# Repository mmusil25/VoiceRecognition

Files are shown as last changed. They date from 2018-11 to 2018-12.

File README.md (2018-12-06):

# Voice Recognition Lock Box

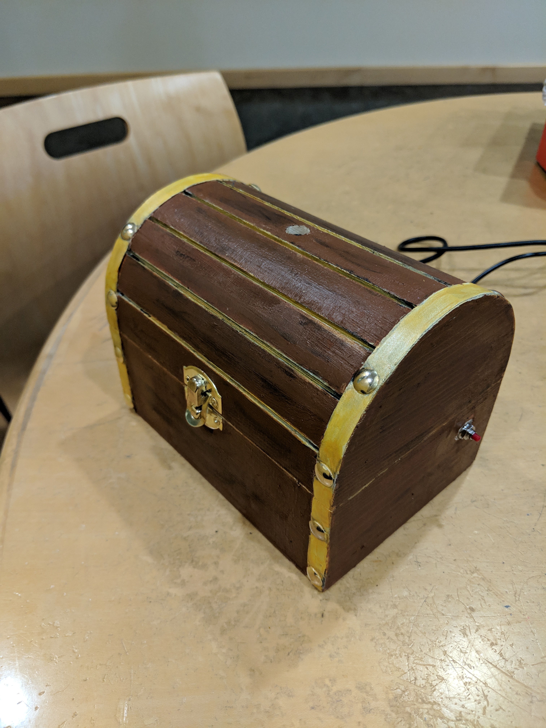
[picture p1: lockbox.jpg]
The Finished Lockbox


### Team Members

Mark Musil (mmusil@pdx.edu), Amanda Voegtlin (voegtlin@pdx.edu), Samantha Fink (scleary@pdx.edu), Rawan Abdo (rabdo@pdx.edu)

## Project Description

For the Portland State University pre-capstone class (ECE 411) the team designed a voice-activated lockbox that can be used to protect belongings. Using the open source [speech-to-text library uSpeech] (https://github.com/arjo129/uSpeech) an AtMega32U4 was programmed to activate a solenoid in response to the diction of a password ("shore"). The potential market for such a product is adolescents with small belongings such as jewelry or diaries that they wish to protect. 

Please see the presentation file "Presentation_Group3.pdf" for a thorough description including block diagrams, functional flowcharts and more.

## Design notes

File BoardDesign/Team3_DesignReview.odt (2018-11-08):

Schematic and Board Layout Design Review Notes

TEAM BEING REVIEWED: TEAM #3

REVIEWING TEAM: TEAM #11

DATE: 11/7/18

Note: (D) = dealt with

- SCHEMATIC
  - CRITICAL
    - (D) Junction dot out of RESET microprofessor button
    - (D) RESET needs a 10k pull up
    - (D) What is UVCC?
    - (D) Add 100nF caps to VCC,VCC1,AVCC,AVCC1
    - (D) Double check UCAP
    - Microphone
    - (D) How much current does the servo need?
    - (D) Remove the regulator
    - (D) Use a wall wart for the servo
      - If using wall wart to power board, need diode from processor to servo.
    - Confirm HWB function and confirm current wiring is correct.
  - MAJOR
    - (D) Add value/name to IC1
    - (D) Use 1 – 3 mA for the LEDs
    - Rearrange wires and add busses for readability.
  - MINOR
    - (D) Change font to info layer
    - (D) Go for right angles
    - (D) Do I need a buffer for the microphone output? Is that output 0 – 3.3V? Check datasheet
    - Statement “all surface mount components are …”
    - Does it use arduino?
    - Test Points Everywhere
    - Label VCC as 5V
- LAYOUT
  - CRITICAL
    - Determine if VCC line width is correct.
    - Align N$13 signal wire to lead straight into pin on processor.
  - MAJOR
    - Move/re-arrange some wires for readability.
  - MINOR
    - None.
- Bill of Materials (BOM)
  - No issues

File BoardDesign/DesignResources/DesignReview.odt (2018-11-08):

Schematic and Board Layout Design Review Notes

TEAM BEING REVIEWED: Team 3

REVIEWING TEAM: Andrew Greenberg (Schematic)/

DATE: November 1st, 2018

Instructions:

1. Reviewed team explains the concept of operation of the project.
2. Reviewer reads through schematic, layout, and BOM attempting to answer basic questions such as: what is the power supply? What is this IC and what does it do? Does the layout make sense?
3. Reviewer reads through schematic, layout, and BOM looking for best practices, such as: Are there enough bypass caps? Are the traces the right thickness?
  a. Reviewers are encouraged to use the Schematic and Layout Checklists that are posted on the D2L site.
4. One person on the reviewed team interacts and answers reviewer’s questions. A different person on the reviewed team takes notes, organized in the format below.
  Note: (D) = dealt with
- SCHEMATIC
  - CRITICAL
    - (D) Junction dot out of RESET microprofessor button
    - (D) RESET needs a 10k pull up
    - (D) What is UVCC?
    - (D) Add 100nF caps to VCC,VCC1,AVCC,AVCC1
    - (D) Double check UCAP
    - Microphone
    - (D) How much current does the servo need?
    - (D) Remove the regulator
    - (D) Use a wall wart for the servo
  - MAJOR
    - (D) Add value/name to IC1
    - (D) Issue 2
  - MINOR
    - (D) Change font to info layer
    - (D) Go for right angles
    - (D) Do I need a buffer for the microphone output? Is that output 0 – 3.3V? Check datasheet
    - (D) Test Points Everywhere
    - (D) Label VCC as 5V
    - Add note saying “All caps are ….”
- LAYOUT
  - CRITICAL
    - Issue 1
    - Issue 2
  - MAJOR
    - Issue 1
    - Issue 2
  - MINOR
    - Issue 1
    - Issue 2
- Bill of Materials (BOM)
  - Issue 1
  - Issue 2

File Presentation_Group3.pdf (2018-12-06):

# Voice Recognition Project Team #3

ECE 411 Practicum
Mark Musil, Rawan Abdo, Samantha Fink, Amanda Voegtlin

### Overview of Problem

- Adolescents want to secure small items in their home but can not find anywhere to do so.
- Must be secure enough for small keepsakes, diaries, etc.
- Not a high security system.
- Must be secure and trendy.

### Project Choice Decision Matrix

| Option 1 - Voice Activated Lock Box | Option 2 -Theremin Lock | Option 3 -Ocarina Lock | Option 4 -Rhythm Lock
Doability (Hardware) | 8 | 7 | 8 | 4
Doability (Software) | 5 | 5 | 7 | 6
Affordability | 8 | 6 | 6 | 5
Interest | 9 | 5 | 8 | 5
Prior Experience | 7 | 5 | 6 | 4
Sum | 37 | 28 | 35 | 24
Rank | 1 | 3 | 2 | 4
Status | Chosen | No | No | No

### Concept of Operation - Voice Activated Lockbox

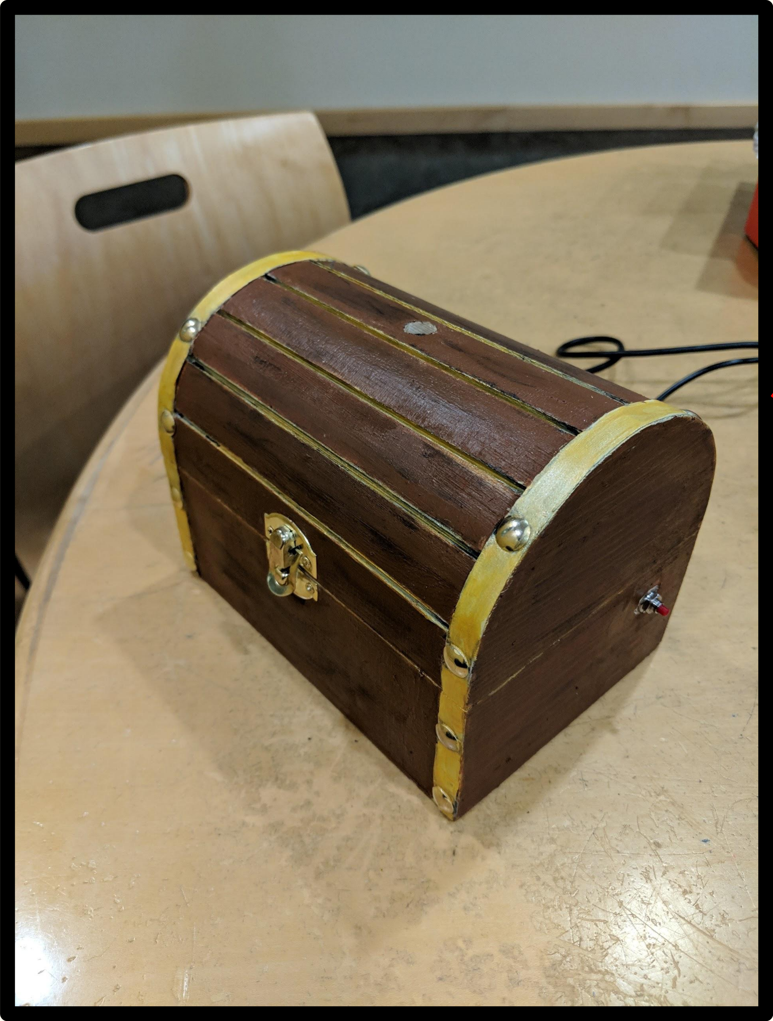
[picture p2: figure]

1. Locked state: Solenoid keeps lid
closed.
2. User input: Password spoken into microphone
3. Device output: Solenoid retracts and box is open
4. User input: Close box, press reset switch, solenoid engages lock.

User Input:
“Shore”

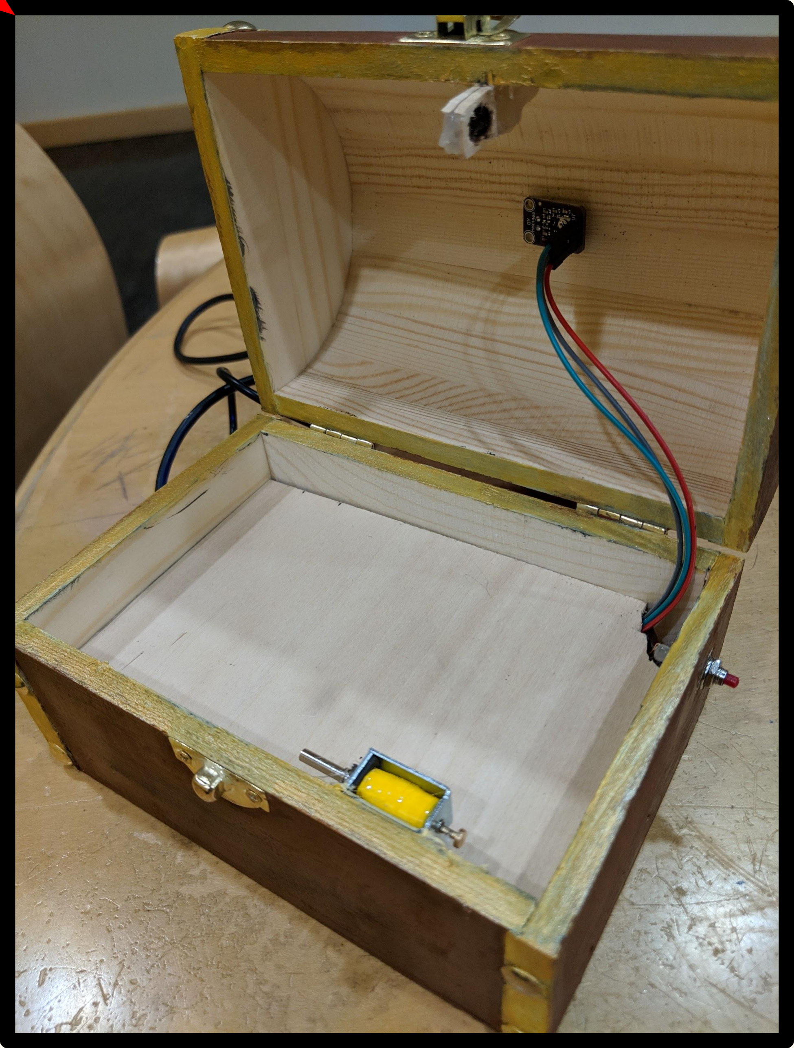
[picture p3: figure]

### Level 0 Block Diagram

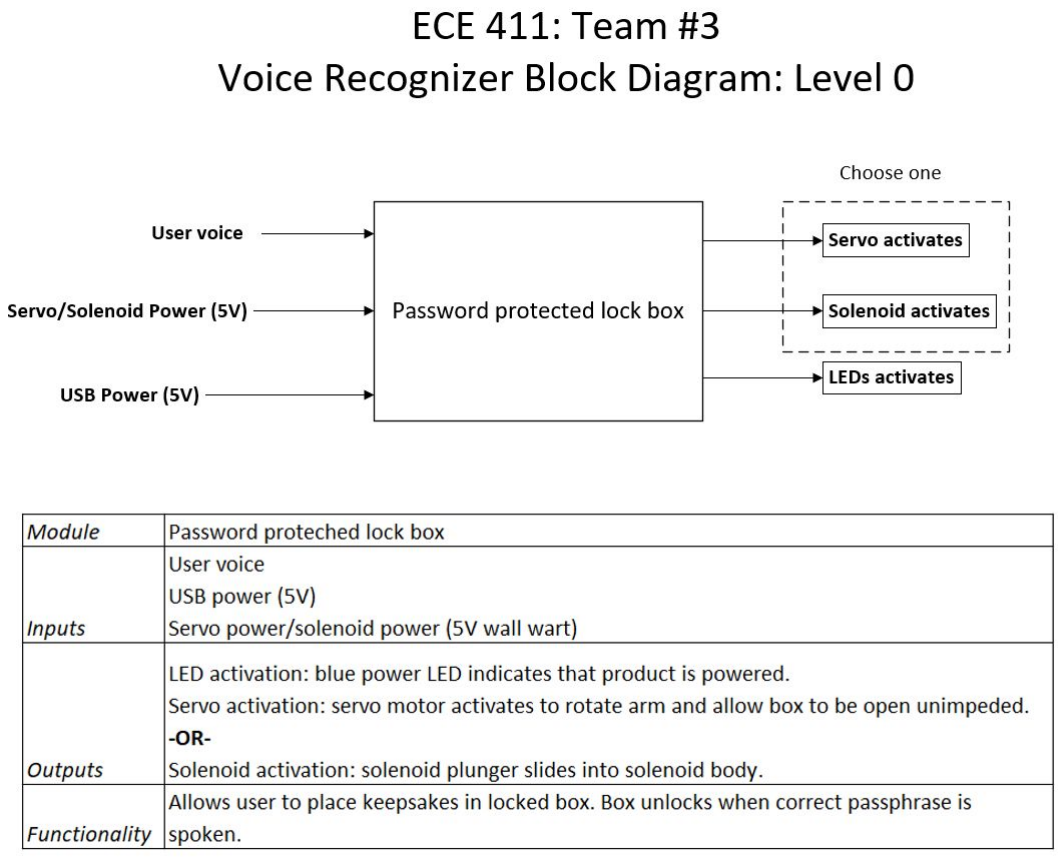
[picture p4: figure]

### Level 1 Block Diagram

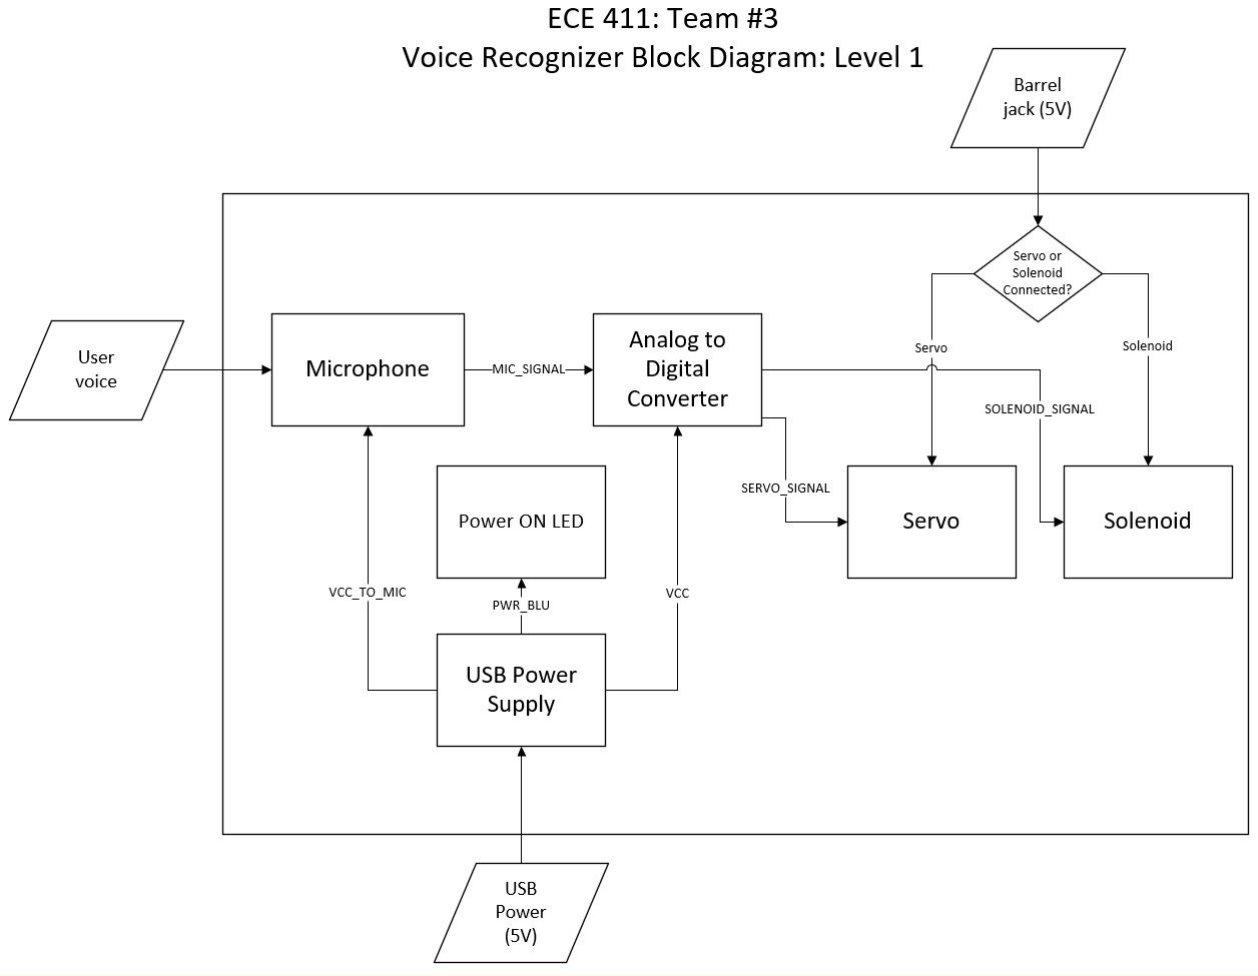
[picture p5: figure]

### Overview of Schematic - Full Picture

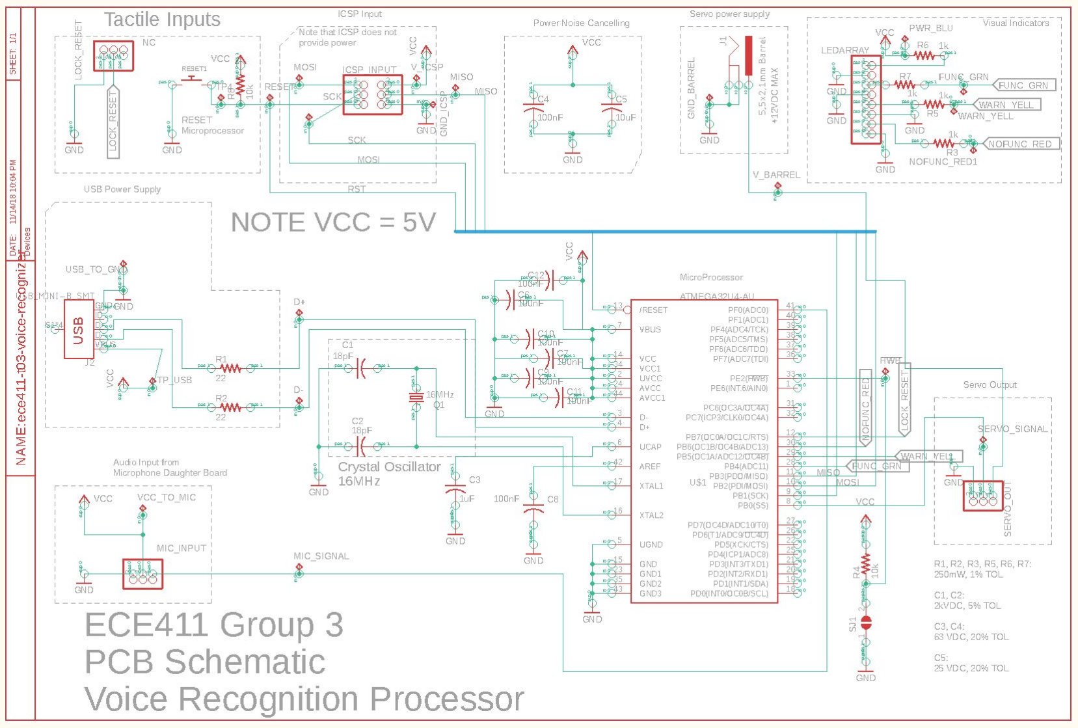
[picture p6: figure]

### Overview of Schematic - Power

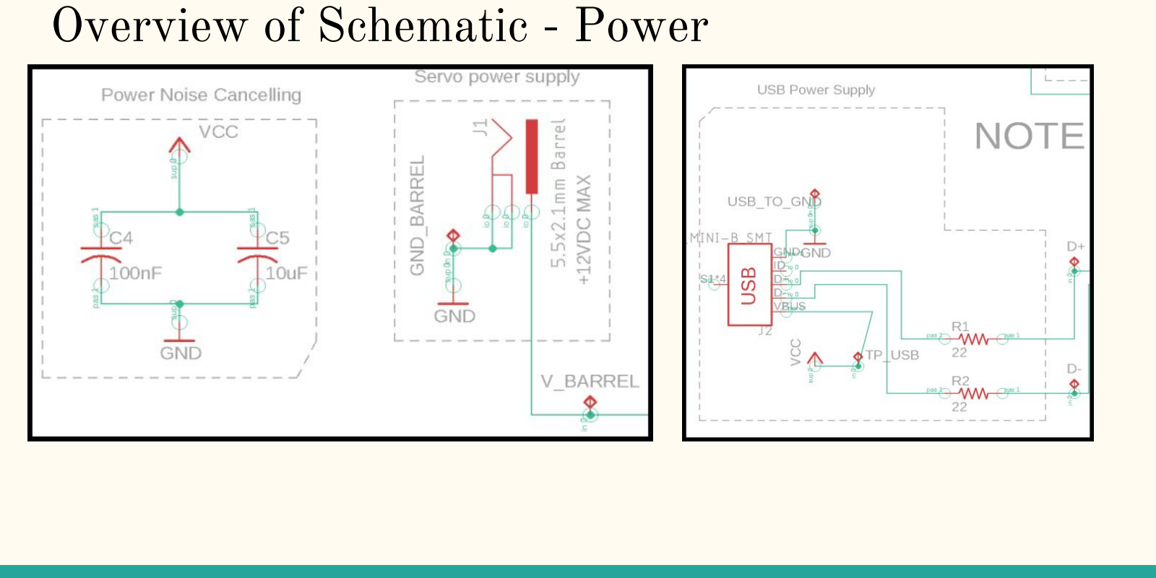
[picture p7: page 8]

### Overview of Schematic - Programming Interface

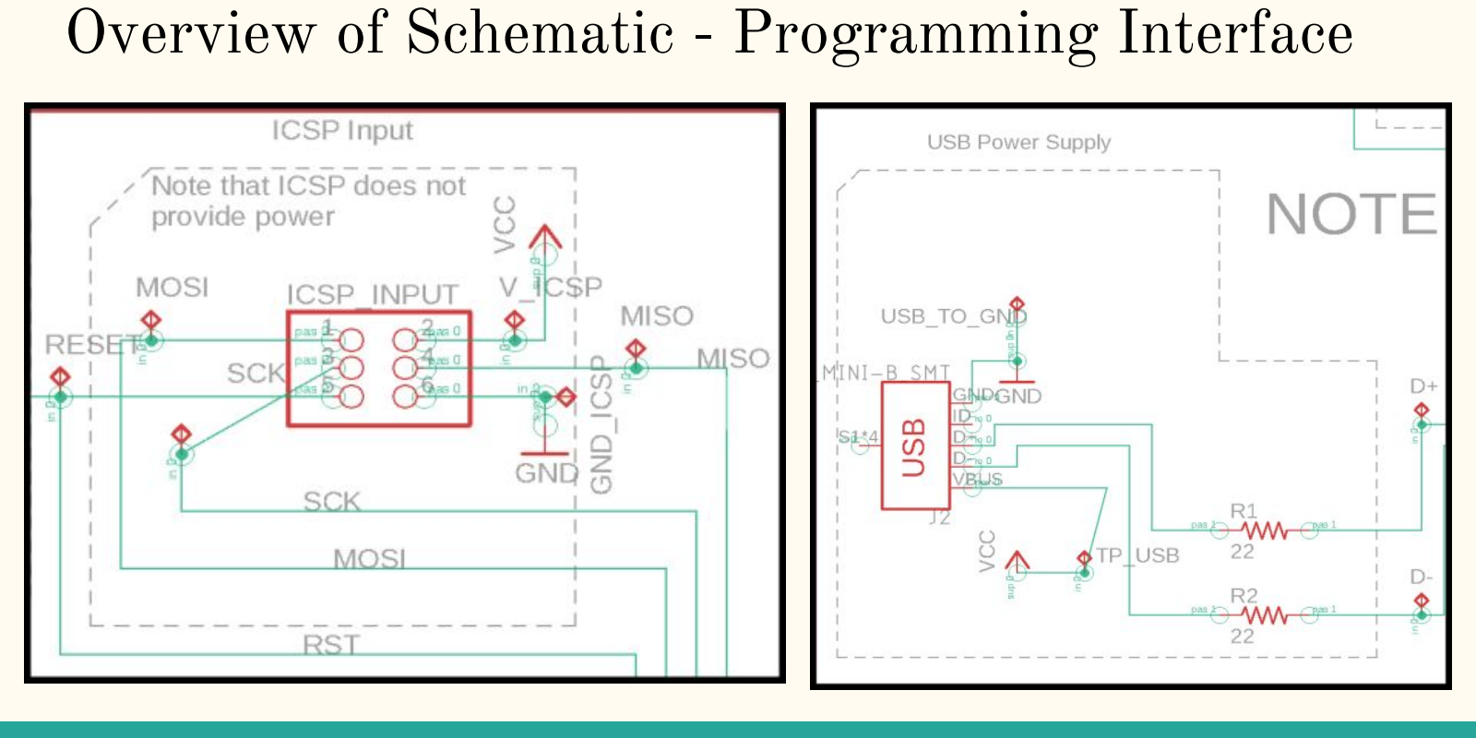
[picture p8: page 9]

### Overview of Schematic - Inputs

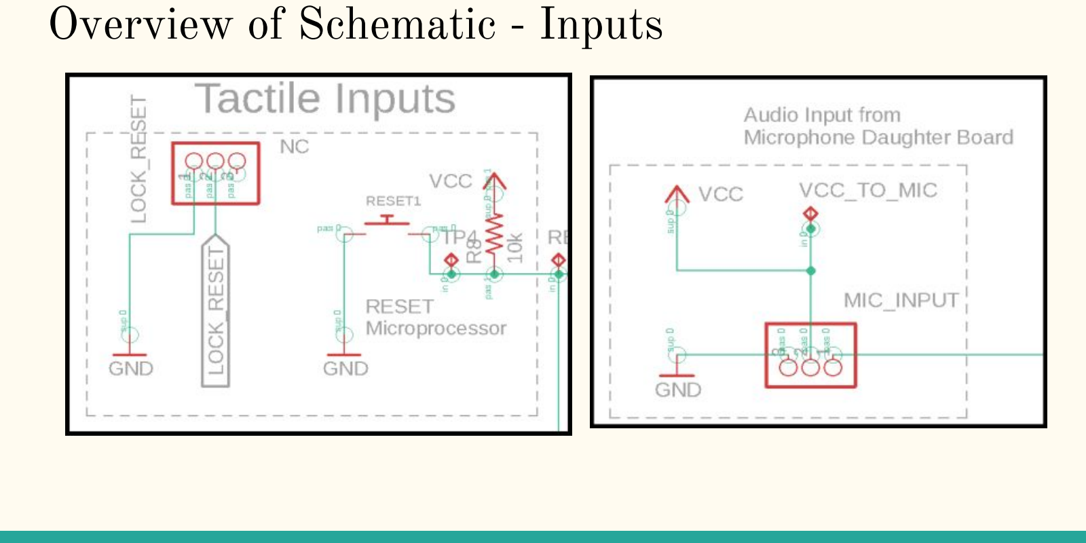
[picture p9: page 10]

### Overview of Schematic - Processor

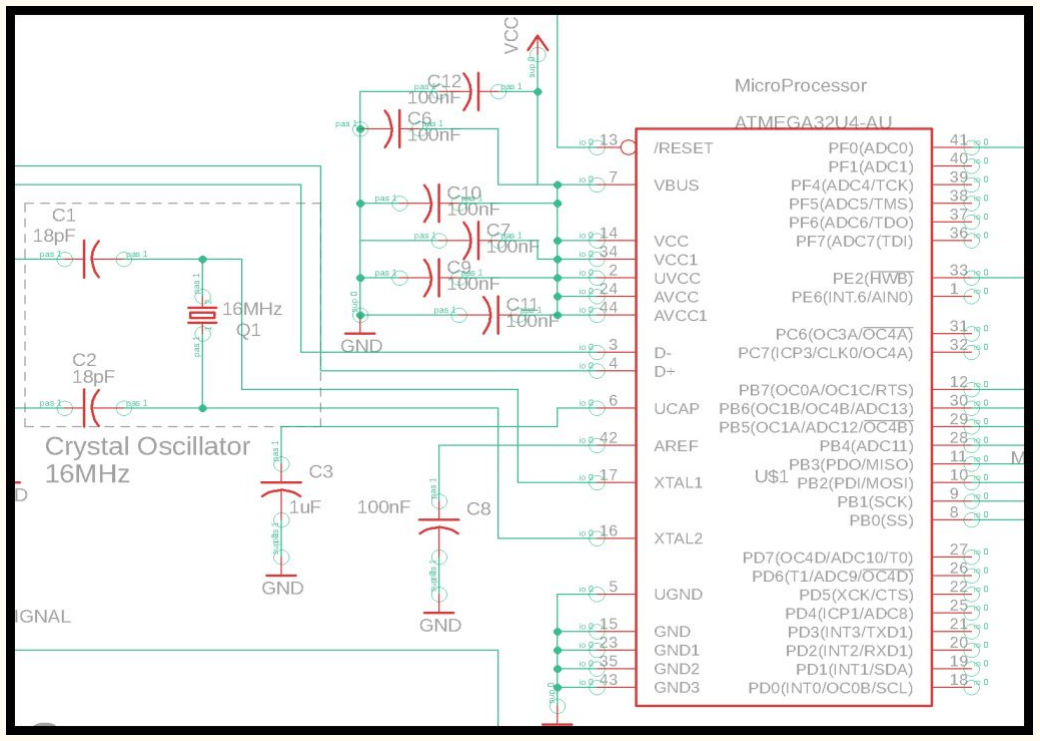
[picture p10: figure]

### Overview of Schematic - Outputs

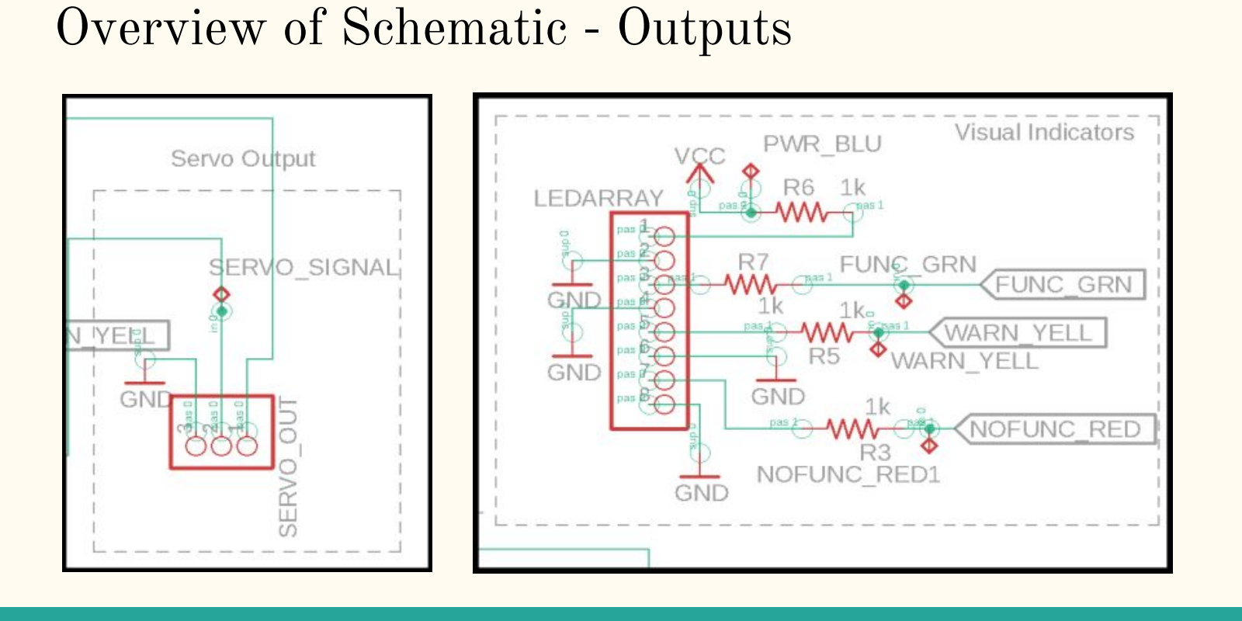
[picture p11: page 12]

### Overview of Layout - Full Picture

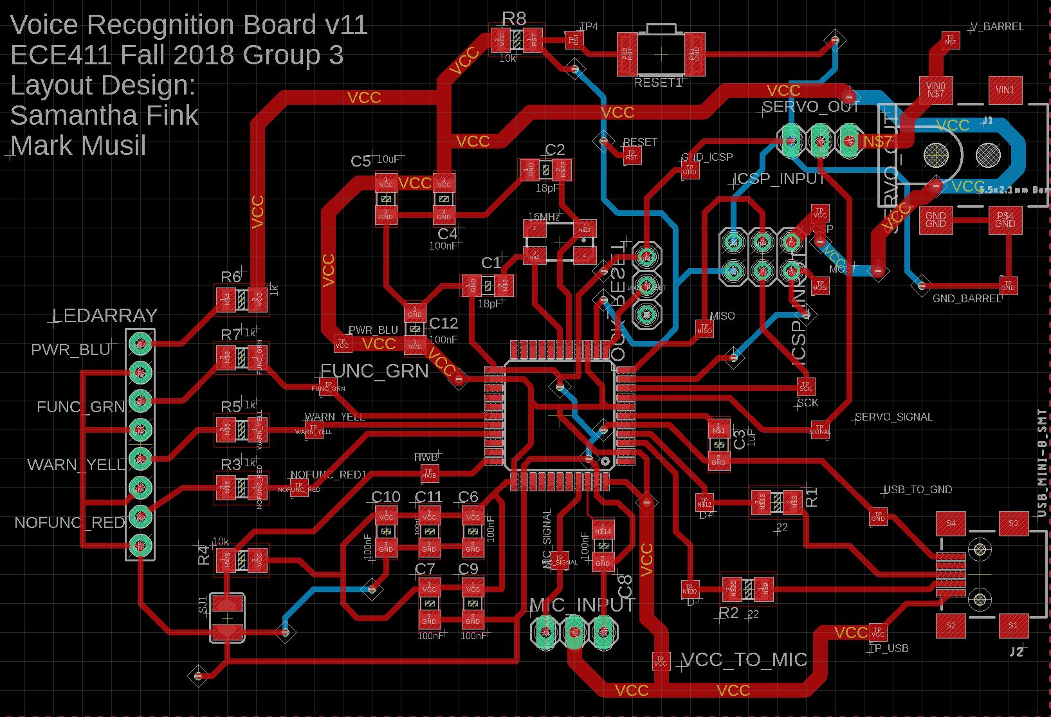
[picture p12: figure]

### Overview of Layout - Power

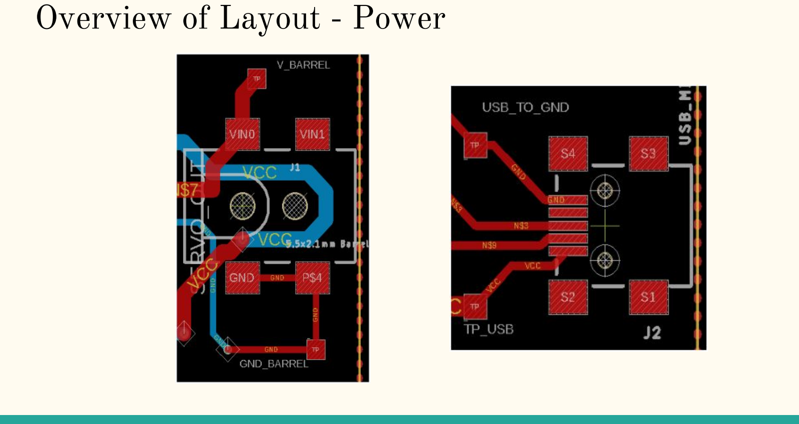
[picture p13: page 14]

### Overview of Schematic - Programming Interface

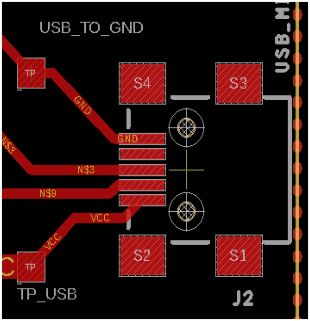
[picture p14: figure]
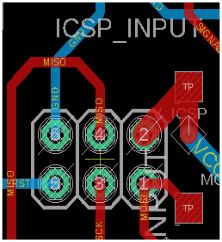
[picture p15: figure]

### Overview of Schematic - Inputs

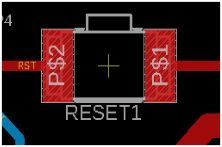
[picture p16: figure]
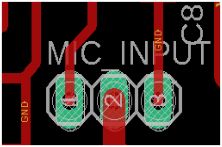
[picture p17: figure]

### Overview of Schematic - Processor

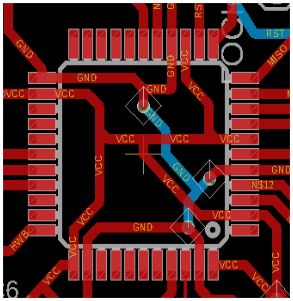
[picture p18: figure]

### Overview of Schematic - Outputs

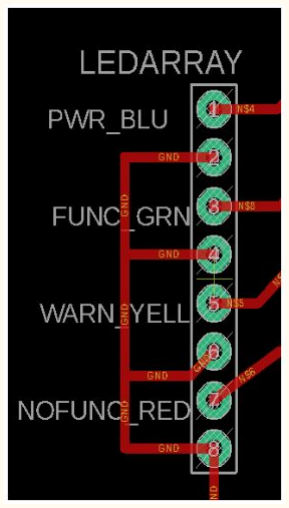
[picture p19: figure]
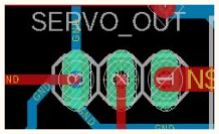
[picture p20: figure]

### Functionality Flowchart

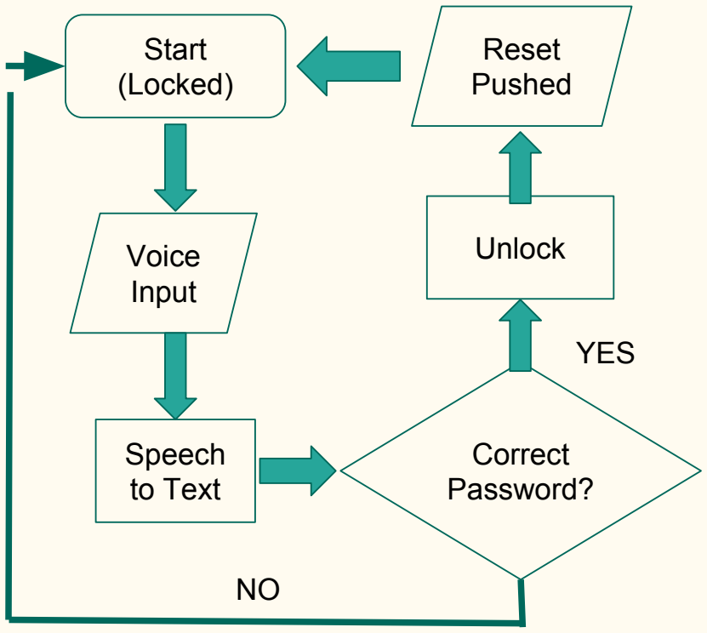
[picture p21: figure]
Start (Locked); Voice Input; Speech to Text; Correct Password?; YES; Unlock; Reset Pushed

### IP Used

- CAD
- EagleCAD was used for the schematic and layout design
- Firmware
- An open source library called “µSpeech” (written by Arjo Chakravarty) is used to analyze the phonemes from the user input.

### Bill of Materials

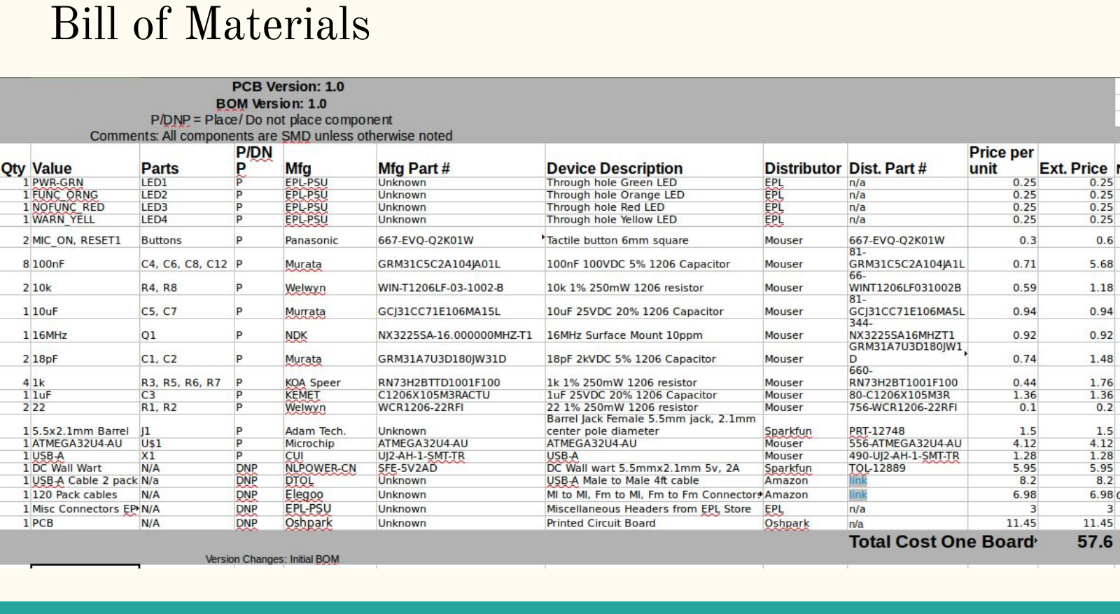
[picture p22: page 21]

Test Plan #1: Initial Power Up of Practicum Project

Objective: to test if board is powered up. The board should be connected to the board and the solenoid should be in the locking position.

Test Procedure: Plug USB connector to laptop to see if blue light is on. If light is on board is powered up.

If light does not turn on:
- Probe the board and check connections.
- Run simple test code (LED blink) to determine if coding issue.

### Test Plan #2: Prototype System (Arduino Uno)

Objective: To test the phoneme recognition. When microphone is powered, solenoid should activate when user speaks password (“shore”) into microphone.

Test procedure: Make sure blue light is on. Say the specified word.

If solenoid is not activated:
- Try repeating the word
- Modify the phoneme sum and other indicators.
- Use debugger that is provided in the arduino uno to figure out why it is not unlocking.

### Gantt Chart

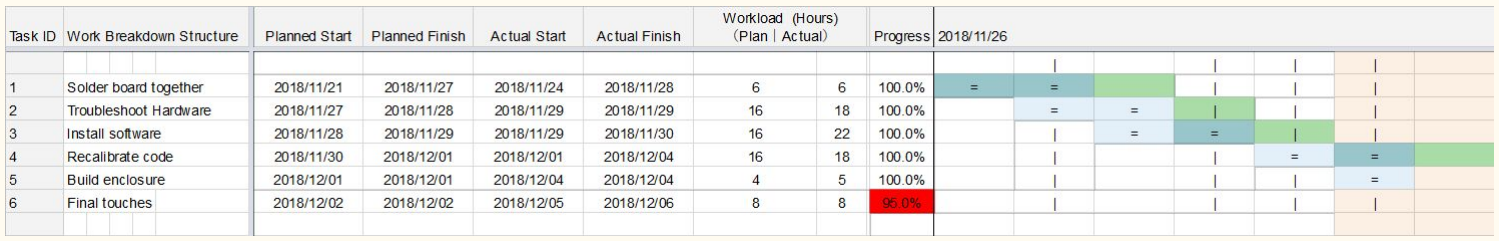
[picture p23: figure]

- Increasing the accuracy of the phoneme recognition.
- This can be done by using a different microphone or a faster processor.
- Reinforcing mechanical strength of the lock and chest.
- Catering aesthetic to the target market’s preferences.

### What is left to do?

### What have we learned as a team?

- We learned how to communicate and split up work accordingly.
- It is critical to record all purchases so that individuals are reimbursed fairly
- Success and failure should come in equal amounts for the best team cohesion

### What have we learned individually?

- Amanda:
- Mark: Test points should be at every node for ease of debugging.
- Rawan:
- Sam: how to use EAGLE (for schematics and PCB routing), new soldering techniques.

# The End Questions?

Link to GitHub (https://github.com/mmusil25/VoiceRecognition)

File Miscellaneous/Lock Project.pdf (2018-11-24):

Rawan Abdo
Amanda Voegtlin
Samantha Fink
Mark Musil
Group 3 Practicum Ideas

Our three choices consist of these projects:

(CHOSEN) Secret Password Lock: Phoneme-activated lock box. Using the open source uSpeech software for microcontrollers, which is a simple phoneme-parsing software, we would code a servo lock to respond to the presence of a phrase or word. The lock, attached to the frame of a small box, would protect the contents until its microphone detected the presence of the word. The user base would be either consumers or industry as both domains have good reason to have a password protected lockbox.

Sensor: Microphone
Controller: ATMEGA 32u4
Actuator: Servo lock

Theremin Lock: Light/Tone activated lock box. Using simple components to generate a theremin, we will make a lock that responds to the generation of certain tones. Since playing a theremin involves waving your hand through a field to generate tones, we are effectively making a lockbox that opens to a series of gestures, with the tones creating feedback to help the user. Software would interpret the sounds through a microphone and identify if the correct ones were received, and then trigger a GPIO pin signal to a servo lock. The user base would be either consumers or industry as both domains have good reason to have a password protected lockbox.

Sensor: Microphone, photocell
Controller: ATMEGA 32u4
Actuator: Servo lock

Ocarina Lock: Music activated lock box. Using the same basic structure as the theremin lockbox, but without the theremin. This would still be a lockbox that opens to a series of tones, but the tones could be generated by any instrument. (In our case, an ocarina.) Software would interpret the sounds through a microphone and identify if the correct ones were received, and then trigger a GPIO pin signal to a servo lock.The user base would be either consumers or industry as both domains have good reason to have a password protected lockbox.
Sensor: Microphone
Controller: ATMEGA 32u4
Actuator: Servo lock

All of them have similar foundation but the complexity of the implementation of the software will differ slightly. We will begin looking into the secret password lock and if anything falls through, switching to any of the two other projects should be no problem. If we are ahead of schedule, we would attempt to include a response to music in our Secret Password lockbox.

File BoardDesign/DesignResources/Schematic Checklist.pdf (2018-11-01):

### Mostly Generic Schematic Checklist

v2017-10-19
From github.com/andrewgreenberg
- Visual Design
- Power supplies use supply symbols, not wires
- Positive supplies point up, and negative supplies/ground point down
- Optional: Groups of nets above about ≥ 4 nets collected into buses
- Component symbols are symbols, not the physical package's order and arrangement
- All nets descriptively named
- Net “stubs” use an off-sheet type of label (“XREF” in EAGLE)
- Blocks in your schematic clearly labeled
- There's a frame around the schematic
- It's clear where your power is coming from
- It's clear what your power input requirements are
- Data flow (inputs, outputs) are clear and labeled
- Part values
- Special case capacitors marked with power and tolerance
- Capacitors have the appropriate voltage
- Power dissipation checked in all of your resistors
- Special case resistors marked with power and tolerance
- Check that your specialized parts are in stock at a distributor
- Electrical Rule checks
- All of your components have values (including “NP” for "No Place")
- All inputs have the correct voltage levels
- All outputs have the correct load impedance
- MOSFETs oriented correctly, including the body diode
- No unapproved errors OR warnings in the ERC
- Your schematic is peer reviewed by at least two different people not involved in the design.
- Double check your approved errors, looking for anomalies and possible errors.
- Best Practices
- Small, low ESR (e.g., ceramic) bypass capacitors on ALL IC supplies
- Large bypass (e.g., electrolytic) capacitors on your board at the power connector and regulator IC.
- Design for Test
■ Place test points on critical signals
■ Add debugging hardware (e.g., test switches, LEDs, scope probe points, etc)
- Design for Fail
■ Group components in separable modular blocks, use zero ohm resistors as jumpers
- Design for Manufacturing
■ Place programming connectors and DOUBLE CHECK their pinouts
■ Double check your part numbers and the actual package names and dimensions.

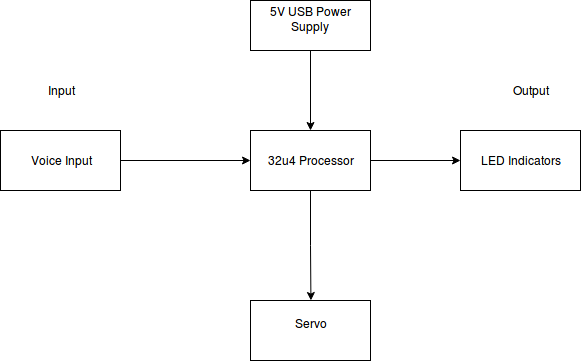
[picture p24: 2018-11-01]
BoardDesign/eagleFiles/SystemArchitecture.png

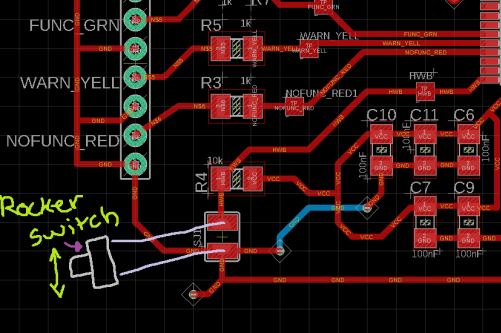
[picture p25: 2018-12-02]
BoardDesign/DesignResources/rocker_switch.png

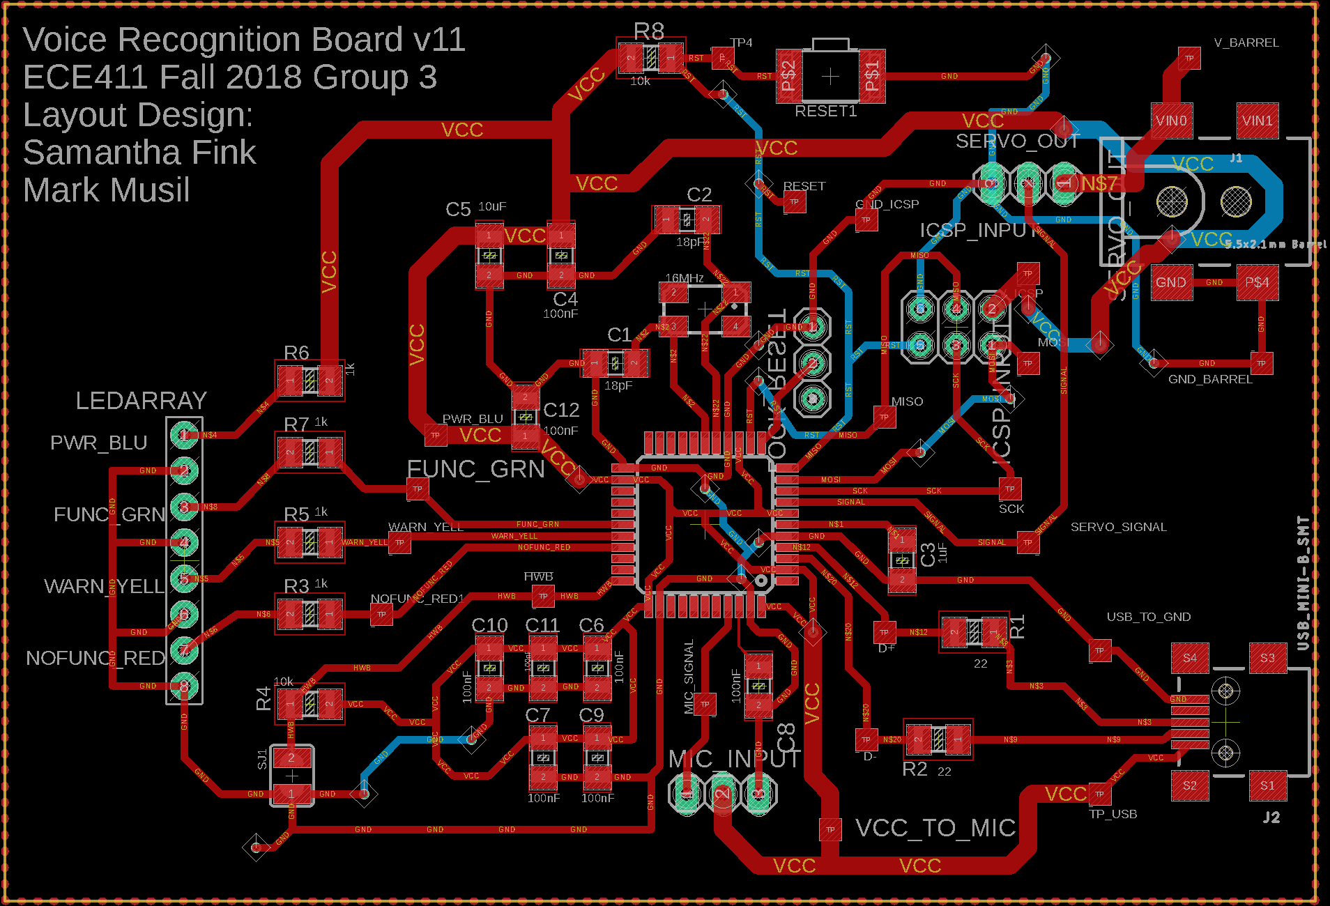
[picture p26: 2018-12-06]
layout.png

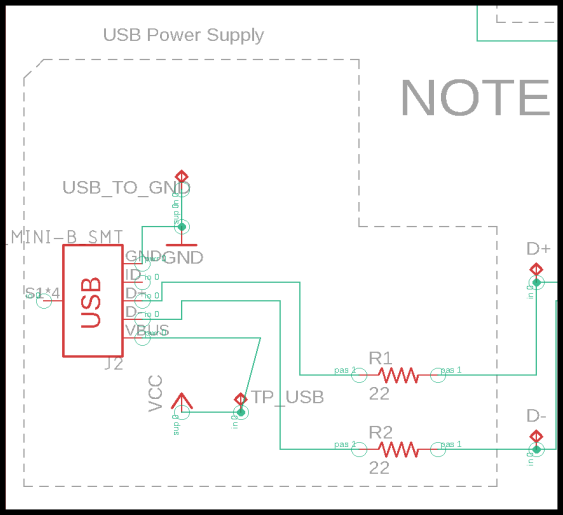
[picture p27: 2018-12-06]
Miscellaneous/schem-prog1.png

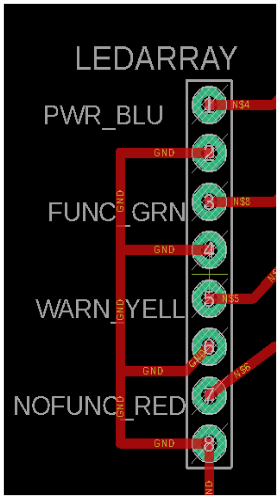
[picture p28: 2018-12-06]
Miscellaneous/layout-outputs2.png

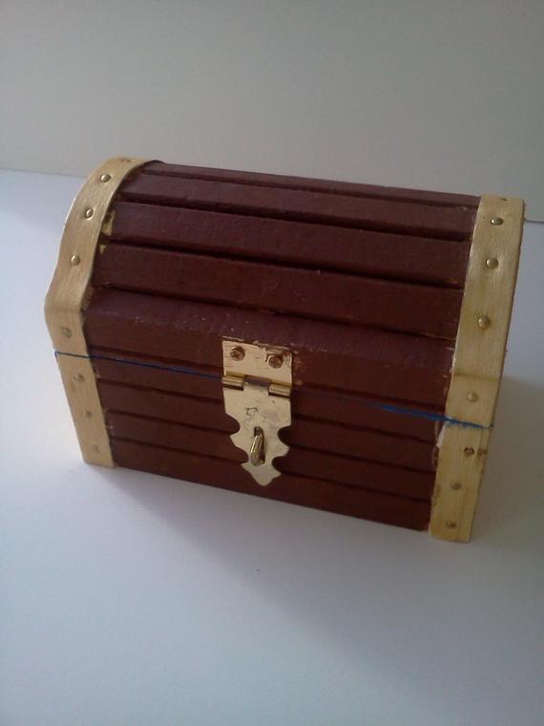
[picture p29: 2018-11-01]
Miscellaneous/Aesthetics/il_570xN.601151211_lxop.jpg

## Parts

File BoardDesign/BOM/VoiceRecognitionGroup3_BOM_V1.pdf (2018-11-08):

VoiceRecognitionGroup3

### Bill of materials for Group 3, Voice Recognition Project Source file: VoiceRecognitionGroup.sch Source File Last modified November 3rd 2018

## PCB Version: 1.0

### BOM Version: 1.0 P/DNP = Place/ Do not place component Comments: All components are SMD unless otherwise noted

Qty Value | Parts | P/DNP Mfg
1 PWR-BLU | LED1 | P | Dialight
1 FUNC_GRN | LED2 | P | Dialight
1 NOFUNC_RED | LED3 | P | Dialight
1 WARN_YELL | LED4 | P | Dialight
2 MIC_ON, RESET1 | Buttons | P | Panasonic
8 100nF | C4, C6, C8, C12 | P | Murata
2 10k | R4, R8 | P | Welwyn
1 10uF | C5, C7 | P | Murrata
1 16MHz | Q1 | P | NDK
2 18pF | C1, C2 | P | Murata
4 1k | R3, R5, R6, R7 | P | KOA Speer
1 1uF | C3 | P | KEMET
2 22 | R1, R2 | P | Welwyn
1 5.5x2.1mm Barrel | J1 | P | Adam Tech.
1 ATMEGA32U4-AU | U$1 | P | Microchip
1 USB-A | X1 | P | CUI
1 DC Wall Wart | N/A | DNP | NLPOWER-CN
1 USB-A Cable 2 pack | N/a | DNP | DTOL
1 120 Pack cables | N/A | DNP | Elegoo
1 Misc Connectors EPL N/A | DNP | EPL-PSU

Version Changes: Initial BOM

Mfg Part # | Device Description | Distributor
597-6601-607F | 1206 Blue LED | Mouser
599-0281-007F | 1206 Green LED | Mouser
597-6001-607F | 1206 Red LED | Mouser
597-6401-607F | 1206 Yellow LED | Mouser
| Tactile button 6mm square | Mouser
GRM31C5C2A104JA01L | 100nF 100VDC 5% 1206 Capacitor | Mouser
WIN-T1206LF-03-1002-B | 10k 1% 250mW 1206 resistor | Mouser
GCJ31CC71E106MA15L | 10uF 25VDC 20% 1206 Capacitor | Mouser
NX3225SA-16.000000MHZ-T1 | 16MHz Surface Mount 10ppm | Mouser
GRM31A7U3D180JW31D | 18pF 2kVDC 5% 1206 Capacitor | Mouser
RN73H2BTTD1001F100 | 1k 1% 250mW 1206 resistor | Mouser
C1206X105M3RACTU | 1uF 25VDC 20% 1206 Capacitor | Mouser
WCR1206-22RFI | 22 1% 250mW 1206 resistor | Mouser
Unknown | | Sparkfun
ATMEGA32U4-AU | ATMEGA32U4-AU | Mouser
UJ2-AH-1-SMT-TR | USB-A | Mouser
SFE-5V2AD | DC Wall wart 5.5mmx2.1mm 5v, 2A | Sparkfun
Unknown | USB-A Male to Male 4ft cable | Amazon
Unknown | Ml to Ml, Fm to Ml, Fm to Fm Connectors | Amazon
Unknown | Miscellaneous Headers from EPL Store | EPL

667-EVQ-Q2K01W

Barrel Jack Female 5.5mm jack, 2.1mm center pole diameter

Dist. Part # | | Ext. Price
645-597-6601-607F | 0.9 | 0.9
645-599-0281-007F | 0.51 | 0.51
645-597-6001-607F | 0.72 | 0.72
645-597-6401-607F | 0.72 | 0.72
667-EVQ-Q2K01W | 0.3 | 0.6
| 0.71 | 5.68
| 0.59 | 1.18
| 0.94 | 0.94
| 0.92 | 0.92
| 0.74 | 1.48
| 0.44 | 1.76
80-C1206X105M3R | 1.36 | 1.36
756-WCR1206-22RFI | 0.1 | 0.2
PRT-12748 | 1.5 | 1.5
556-ATMEGA32U4-AU | 4.12 | 4.12
490-UJ2-AH-1-SMT-TR | 1.28 | 1.28
TOL-12889 | 5.95 | 5.95
| 8.2 | 8.2
| 6.98 | 6.98
| 3 | 3
Total Cost: | | 48

## Price per unit

81-
GRM31C5C2A104JA1L
66-
WINT1206LF031002B
81-
GCJ31CC71E106MA5L
344-
NX3225SA16MHZT1
81-
GRM31A7U3D180JW1D
660-
RN73H2BT1001F100

link (https://www.amazon.com/dp/B074GY5B1H/ref=twister_B07K88TLT5?_encoding=UTF8&psc=1#)
link (https://www.amazon.com/Elegoo-EL-CP-004-Multicolored-Breadboard-arduino/dp/B01EV70C78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)

### Notes

Only 1 bundled need for all 4 boards

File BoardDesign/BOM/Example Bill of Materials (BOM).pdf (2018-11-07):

Bill Of Materials for [Team # and project name]
source file: [name of EAGLE schematic file]
Last modified: [Date]
PCB version: [Version] | P/DNP = | Place/Do Not Place component
BOM revision: [Version]
Cnt | Part References | P/DNP Mfg | Mfg PN
2 R3, R5 | P | Samsung | RC1005F6653CS
1 X1 | P | ECS Inc. | ECS-160-10-36Q-ES-TR
1 U1 | P | ST | STM32F042K6T7
Ver # | Changed in version
1 | Initial BOM.

Description | Distributor | Dist. PN | Cost Ea. Cost Ext.
0 ohm 1% 0402 resistor | Digikey | 1276-4275-1-ND | 0.08 | 0.16
16MHz crystal 2.5x2mm package | Digikey | XC2181CT-ND | 1.14 | 1.14
IC MCU 32BIT 32KB FLASH 32LQFP | Digikey | 497-14647-ND | 2.83 | 2.83
TOTAL COST: | $ | 4.13

Notes

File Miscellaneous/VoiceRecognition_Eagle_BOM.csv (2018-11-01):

Qty | Value | Device | Package | Parts | Description | MF | MPN | OC_FARNELL | OC_NEWARK | SPICEPREFIX
4 |  | LEDCHIPLED_1206 | CHIPLED_1206 | FUNCTION-GRN, NOFUNCTION-RED, POWER-BLU, WARNING-ORNG | LED
1 |  | MCP1700INLINE | TO92-INLINE | IC1 | VOLTAGE REGULATOR
2 |  | PINHD-1X3 | 1X03 | JP2, JP3 | PIN HEADER
1 |  | PINHD-2X3 | 2X03 | JP1 | PIN HEADER
1 |  | PTCFUSE-1206 | R1206 | F1 | PTC fuses, resettable thermistors
1 |  | SJW | SJW | SJ1 | SMD solder JUMPER
1 |  | SWITCH_PUSHBUTTONC&K_KSS | BTN_CK_KSS | RESET | Buttons
2 | 100nF | C-USC1206 | C1206 | C3, C4 | CAPACITOR, American symbol |  |  |  |  | C
1 | 10k | R-US_M1206 | M1206 | R4 | RESISTOR, American symbol |  |  |  |  | R
1 | 10uF | C-USC1206 | C1206 | C5 | CAPACITOR, American symbol |  |  |  |  | C
1 | 150\ | R-US_M1206 | M1206 | R3 | RESISTOR, American symbol |  |  |  |  | R
1 | 1600 | R-US_M1206 | M1206 | R5 | RESISTOR, American symbol |  |  |  |  | R
1 | 16MHz | CRYSTALCTS406 | CTS406 | Q1 | CRYSTAL |  |  | unknown | unknown
2 | 18pF | C-USC1206 | C1206 | C1, C2 | CAPACITOR, American symbol |  |  |  |  | C
2 | 22 | R-US_M1206 | M1206 | R1, R2 | RESISTOR, American symbol |  |  |  |  | R
2 | 90 | R-US_M1206 | M1206 | R6, R7 | RESISTOR, American symbol |  |  |  |  | R
1 | ATMEGA32U4-AU | ATMEGA32U4-AU | TQFP44 | U$1 | http://www.ladyada.net/library/eagle
1 | USB-A | USB-A | MOLEX_480371000 | X1 | USB type A 'plug'

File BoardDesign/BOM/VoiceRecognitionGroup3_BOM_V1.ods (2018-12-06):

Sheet: VoiceRecognitionGroup3
Bill of materials for Group 3, Voice Recognition Project
Source file: VoiceRecognitionGroup.sch Source File
Last modified November 3rd 2018
 | PCB Version: 1.0
BOM Version: 1.0
P/DNP = Place/ Do not place component
Comments: All components are SMD unless otherwise noted
Qty | Value | Parts | P/DNP | Mfg | Mfg Part # | Device Description | Distributor | Dist. Part # | Price per unit | Ext. Price | Notes
1 | PWR-GRN | LED1 | P | EPL-PSU | Unknown | Through hole Green LED | EPL | n/a | 0.25 | 0.25
1 | FUNC_ORNG | LED2 | P | EPL-PSU | Unknown | Through hole Orange LED | EPL | n/a | 0.25 | 0.25
1 | NOFUNC_RED | LED3 | P | EPL-PSU | Unknown | Through hole Red LED | EPL | n/a | 0.25 | 0.25
1 | WARN_YELL | LED4 | P | EPL-PSU | Unknown | Through hole Yellow LED | EPL | n/a | 0.25 | 0.25
2 | MIC_ON, RESET1 | Buttons | P | Panasonic | 667-EVQ-Q2K01W | Tactile button 6mm square | Mouser | 667-EVQ-Q2K01W | 0.3 | 0.6
8 | 100nF | C4, C6, C8, C12 | P | Murata | GRM31C5C2A104JA01L | 100nF 100VDC 5% 1206 Capacitor | Mouser | 81-GRM31C5C2A104JA1L | 0.71 | 5.68
2 | 10k | R4, R8 | P | Welwyn | WIN-T1206LF-03-1002-B | 10k 1% 250mW 1206 resistor | Mouser | 66-WINT1206LF031002B | 0.59 | 1.18
1 | 10uF | C5, C7 | P | Murrata | GCJ31CC71E106MA15L | 10uF 25VDC 20% 1206 Capacitor | Mouser | 81-GCJ31CC71E106MA5L | 0.94 | 0.94
1 | 16MHz | Q1 | P | NDK | NX3225SA-16.000000MHZ-T1 | 16MHz Surface Mount 10ppm | Mouser | 344-NX3225SA16MHZT1 | 0.92 | 0.92
2 | 18pF | C1, C2 | P | Murata | GRM31A7U3D180JW31D | 18pF 2kVDC 5% 1206 Capacitor | Mouser | 81-GRM31A7U3D180JW1D | 0.74 | 1.48
4 | 1k | R3, R5, R6, R7 | P | KOA Speer | RN73H2BTTD1001F100 | 1k 1% 250mW 1206 resistor | Mouser | 660-RN73H2BT1001F100 | 0.44 | 1.76
1 | 1uF | C3 | P | KEMET | C1206X105M3RACTU | 1uF 25VDC 20% 1206 Capacitor | Mouser | 80-C1206X105M3R | 1.36 | 1.36
2 | 22 | R1, R2 | P | Welwyn | WCR1206-22RFI | 22 1% 250mW 1206 resistor | Mouser | 756-WCR1206-22RFI | 0.1 | 0.2
1 | 5.5x2.1mm Barrel | J1 | P | Adam Tech. | Unknown | Barrel Jack Female 5.5mm jack, 2.1mm center pole diameter | Sparkfun | PRT-12748 | 1.5 | 1.5
1 | ATMEGA32U4-AU | U$1 | P | Microchip | ATMEGA32U4-AU | ATMEGA32U4-AU | Mouser | 556-ATMEGA32U4-AU | 4.12 | 4.12
1 | USB-A | X1 | P | CUI | UJ2-AH-1-SMT-TR | USB-A | Mouser | 490-UJ2-AH-1-SMT-TR | 1.28 | 1.28
1 | DC Wall Wart | N/A | DNP | NLPOWER-CN | SFE-5V2AD | DC Wall wart 5.5mmx2.1mm 5v, 2A | Sparkfun | TOL-12889 | 5.95 | 5.95
1 | USB-A Cable 2 pack | N/a | DNP | DTOL | Unknown | USB-A Male to Male 4ft cable | Amazon | link (https://www.amazon.com/dp/B074GY5B1H/ref=twister_B07K88TLT5?_encoding=UTF8&psc=1) | 8.2 | 8.2
1 | 120 Pack cables | N/A | DNP | Elegoo | Unknown | Ml to Ml, Fm to Ml, Fm to Fm Connectors | Amazon | link (https://www.amazon.com/Elegoo-EL-CP-004-Multicolored-Breadboard-arduino/dp/B01EV70C78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) | 6.98 | 6.98 | Only 1 bundled need for all 4 boards
1 | Misc Connectors EPL | N/A | DNP | EPL-PSU | Unknown | Miscellaneous Headers from EPL Store | EPL | n/a | 3 | 3
1 | PCB | N/A | DNP | Oshpark | Unknown | Printed Circuit Board | Oshpark | n/a | 11.45 | 11.45
 |  |  |  |  |  |  |  | Total Cost One Board: |  | 57.6
Version Changes: Initial BOM

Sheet: SpendingRecord
Date Purchased | Product(s) | Source | Purchaser | Amount | Totals by Purchaser
10/4/2018 | Microphone | EPL | Amanda | $5.00 | Amanda | $5.00
10/11/2018 | Prototype Board, op-amp +shipping | Mouser | Sam | $33.95 | Sam | $33.95
 |  |  |  |  | Mark | $0.00
 |  |  |  |  | Rawan | $0.00
 |  |  | Grand Total | $38.95
 |  |  | Reference
 |  |  | Amanda
 |  |  | Sam
 |  |  | Mark
 |  |  | Rawan

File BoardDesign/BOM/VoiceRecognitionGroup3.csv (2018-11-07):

Qty | Value | Device | Package | Parts | Description | MF | MPN | OC_FARNELL | OC_NEWARK | PROD_ID | SF_ID | SPICEPREFIX | TP_SIGNAL_NAME | VALUE
4 |  | LEDSMT1206 | 1206 | LED2, LED3, LED4, PWR-BLU | LED
2 |  | PINHD-1X3 | 1X03 | JP2, JP3 | PIN HEADER
1 |  | PINHD-2X3 | 2X03 | JP1 | PIN HEADER
1 |  | SJW | SJW | SJ1 | SMD solder JUMPER
2 |  | SWITCH_PUSHBUTTONC&K_KSS | BTN_CK_KSS | MIC_ON, RESET1 | Buttons
4 | 100nF | C-USC1206 | C1206 | C4, C6, C8, C12 | CAPACITOR, American symbol |  |  |  |  |  |  | C
2 | 10k | R-US_M1206 | M1206 | R4, R8 | RESISTOR, American symbol |  |  |  |  |  |  | R
2 | 10uF | C-USC1206 | C1206 | C5, C7 | CAPACITOR, American symbol |  |  |  |  |  |  | C
1 | 16MHz | CRYSTALCTS406 | CTS406 | Q1 | CRYSTAL |  |  | unknown | unknown
2 | 18pF | C-USC1206 | C1206 | C1, C2 | CAPACITOR, American symbol |  |  |  |  |  |  | C
4 | 1k | R-US_M1206 | M1206 | R3, R5, R6, R7 | RESISTOR, American symbol |  |  |  |  |  |  | R
1 | 1uF | C-USC1206 | C1206 | C3 | CAPACITOR, American symbol |  |  |  |  |  |  | C
2 | 22 | R-US_M1206 | M1206 | R1, R2 | RESISTOR, American symbol |  |  |  |  |  |  | R
1 | 5.5x2.1mm Barrel | POWER_JACKSMD | POWER_JACK_SMD | J1 | Power Jack Connector |  |  |  |  | CONN-08106 | PRT-12748 |  |  | 5.5x2.1mm Barrel
1 | ATMEGA32U4-AU | ATMEGA32U4-AU | TQFP44 | U$1 | http://www.ladyada.net/library/eagle
21 | TPTP15SQ | TPTP15SQ | TP15SQ | !HWB, D+, D-, FUNC_GRN, GND_BARREL, GND_ICSP, MIC_SIGNAL, MISO, MOSI, NOFUNC_RED, PWR_BLU, RESET, SCK, SERVO_SIGNAL, TP4, TP7, VCC, VCC_TO_MIC, V_BARREL, V_ICSP, WARN_YELL | Test pad
1 | USB-A | USB-A | MOLEX_480371000 | X1 | USB type A 'plug'

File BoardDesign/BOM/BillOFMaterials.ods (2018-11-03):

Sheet: Final_Product
Bill of materials for Group 3, Voice Recognition Project
 | All components are SMD unless otherwise noted |  |  |  |  | Boards to be ordered: | 1
Description | Notes | Vendor Part # | Mfr Model # | Source | Price per Unit | Quantity per board | Order Quantity | Item Total
uProcessor |  | 556-ATMEGA32U4-AU (https://www.mouser.com/ProductDetail/Microchip-Technology-Atmel/ATMEGA32U4-AU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) | ATMEGA32U4-AU (https://www.mouser.com/ProductDetail/Microchip-Technology-Atmel/ATMEGA32U4-AU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) | link (https://www.mouser.com/ProductDetail/Microchip-Technology-Atmel/ATMEGA32U4-AU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) | $4.12 | 1 | 1 | $4.12
Green LED |  | 645-599-0281-007F | 599-0281-007F | link (https://www.mouser.com/ProductDetail/Dialight/599-0281-007F) | $0.51 | 1 | 1 | $0.51
Blue LED |  | 645-597-6601-607F | 597-6601-607F | link (https://www.mouser.com/ProductDetail/Dialight/597-6601-607F?qs=sGAEpiMZZMseGfSY3csMkR8RaVMxbPqBHeLW7DRhG0M%3D) | $0.90 | 1 | 1 | $0.90
Red LED |  | 645-597-6001-607F | 597-6001-607F | link (https://www.mouser.com/ProductDetail/Dialight/597-6001-607F?qs=sGAEpiMZZMseGfSY3csMkR8RaVMxbPqBDpUEGjhaf0E%3D) | $0.72 | 1 | 1 | $0.72
Yellow LED |  | 645-597-6401-607F | 597-6401-607F | link (https://www.mouser.com/ProductDetail/Dialight/597-6401-607F?qs=sGAEpiMZZMseGfSY3csMkR8RaVMxbPqBUFBdHV7BX30%3D) | $0.72 | 1 | 1 | $0.72
Button Switch |  | 667-EVQ-Q2K01W (https://www.mouser.com/ProductDetail/Panasonic/EVQ-Q2K01W) | EVQ-Q2K01W (https://www.mouser.com/ProductDetail/Panasonic/EVQ-Q2K01W) | link (https://www.mouser.com/ProductDetail/Panasonic/EVQ-Q2K01W) | $0.30 | 2 | 2 | $0.60
10k Resistor |  | 66-WINT1206LF031002B (https://www.mouser.com/ProductDetail/Welwyn-Components-TT-Electronics/WIN-T1206LF-03-1002-B) | WIN-T1206LF-03-1002-B (https://www.mouser.com/ProductDetail/Welwyn-Components-TT-Electronics/WIN-T1206LF-03-1002-B) | link (https://www.mouser.com/ProductDetail/Welwyn-Components-TT-Electronics/WIN-T1206LF-03-1002-B) | $0.59 | 1 | 1 | $0.59
150 resistor |  | 66-WINT1206LF031500B | WIN-T1206LF-03-1500-B | link (https://www.mouser.com/ProductDetail/Welwyn-Components-TT-Electronics/WIN-T1206LF-03-1500-B) | 0.59 | 2 | 2 | $1.18
100 resistor |  | 652-CRT1206FZ1000ELF | CRT1206-FZ-1000ELF | link (https://www.mouser.com/ProductDetail/Bourns/CRT1206-FZ-1000ELF) | 0.26 | 1 | 1 | $0.26
90.9 resistor |  | 66-WINT1206LF0390R9B | WIN-T1206LF-03-90R9-B | link (https://www.mouser.com/ProductDetail/Welwyn-Components-TT-Electronics/WIN-T1206LF-03-90R9-B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) | $0.59 | 1 | 1 | $0.59
22 Ohm Resistor |  | 756-WCR1206-22RFI (https://www.mouser.com/ProductDetail/Welwyn-Components-TT-Electronics/WCR1206-22RFI) | WCR1206-22RFI (https://www.mouser.com/ProductDetail/Welwyn-Components-TT-Electronics/WCR1206-22RFI) | link (https://www.mouser.com/ProductDetail/Welwyn-Components-TT-Electronics/WCR1206-22RFI) | $0.10 | 2 | 2 | $0.20
16MHz Oscillator |  | 344-NX3225SA16MHZT1 (https://www.mouser.com/ProductDetail/NDK/NX3225SA-16000000MHZ-T1) | NX3225SA-16.000000MHZ-T1 (https://www.mouser.com/ProductDetail/NDK/NX3225SA-16000000MHZ-T1) | link (https://www.mouser.com/ProductDetail/NDK/NX3225SA-16000000MHZ-T1) | $0.92 | 1 | 1 | $0.92
18pF Cap |  | 81-GRM31A7U3D180JW1D (https://www.mouser.com/ProductDetail/Murata-Electronics/GRM31A7U3D180JW31D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) | GRM31A7U3D180JW31D (https://www.mouser.com/ProductDetail/Murata-Electronics/GRM31A7U3D180JW31D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) | link (https://www.mouser.com/ProductDetail/Murata-Electronics/GRM31A7U3D180JW31D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) | $0.57 | 2 | 2 | $1.14
10uF |  | 81-GCJ31CC71E106MA5L (https://www.mouser.com/ProductDetail/Murata-Electronics/GCJ31CC71E106MA15L) | GCJ31CC71E106MA15L (https://www.mouser.com/ProductDetail/Murata-Electronics/GCJ31CC71E106MA15L) | link (https://www.mouser.com/ProductDetail/Murata-Electronics/GCJ31CC71E106MA15L) | $0.94 | 1 | 1 | $0.94
100nf |  | 81-GRM31C5C2A104JA1L (https://www.mouser.com/ProductDetail/Murata-Electronics/GRM31C5C2A104JA01L) | GRM31C5C2A104JA01L (https://www.mouser.com/ProductDetail/Murata-Electronics/GRM31C5C2A104JA01L) | link (https://www.mouser.com/ProductDetail/Murata-Electronics/GRM31C5C2A104JA01L) | $0.71 | 3 | 3 | $2.13
1uF |  | 80-C1206X105M3R | C1206X105M3RACTU | link (https://www.mouser.com/ProductDetail/KEMET/C1206X105M3RACTU) | $1.36 | 3 | 3 | $4.08
Voltage regulator | through hole | 579-MCP1700-5002E/TO | MCP1700-5002E/TO | link (https://www.mouser.com/ProductDetail/Microchip-Technology/MCP1700-5002E-TO) | $0.39 | 1 | 1 | $0.39
USB Type A Female |  | 490-UJ2-AH-1-SMT-TR | UJ2-AH-1-SMT-TR | link (https://www.mouser.com/Connectors/USB-Connectors/_/N-88hmf?P=1z0yy6bZ1z0z7ym&Keyword=USB+type+A+female&FS=True) | $1.28 | 2 | 2 | $2.56
DC Barrel Jack | Sparkfun | PRT-12748 |  | link (https://www.sparkfun.com/products/12748) | $1.50 | 1 | 1 | $1.50
DC 5V wall wart | Sparkfun | TOL-12889 |  | link (https://www.sparkfun.com/products/12889) | $5.95 | 1 | 1 | $5.95
 |  |  |  |  |  | Purchase Sub Total |  | $30.00

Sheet: Prototype
Description | Notes | Mouser Model # | Mfr Model # | Source | Price per Unit | Quantity | Item Total
AVR Adafruit Development Board - 32u4 | SF: purchased 10/11/18 | 485-3677 | 3677 | link (https://www.mouser.com/ProductDetail/Adafruit/3677) | $9.95 | 2 | $19.90
LM386N-3 Audio Amplifier | SF: purchased 10/11/18 | 926-LM386N-3/NOPB | LM386N-3/NOPB | link (https://www.mouser.com/ProductDetail/texas-instruments/lm386n-3-nopb/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) | $1.01 | 6 | $6.06
 |  |  |  |  |  | Purchase Sub Total | $25.96

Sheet: Admin
Date Purchased | Product(s) | Source | Purchaser | Amount | Totals by Purchaser
10/4/2018 | Microphone | EPL | Amanda | $5.00 | Amanda | $5.00
10/11/2018 | Prototype Board, op-amp +shipping | Mouser | Sam | $33.95 | Sam | $33.95
 |  |  |  |  | Mark | $0.00
 |  |  |  |  | Rawan | $0.00
 |  |  | Grand Total | $38.95
 |  |  | Reference
 |  |  | Amanda
 |  |  | Sam
 |  |  | Mark
 |  |  | Rawan

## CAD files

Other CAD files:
BoardDesign/eagleFiles/ece411-t03-voice-recognizer-tcream.dxf
BoardDesign/eagleFiles/ece411-t03-voice-recognizer-bcream.dxf

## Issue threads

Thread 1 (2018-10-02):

Hardware between microphone and AtMega

mmusil25, 2018-10-02:
How do we decide what the algorithm for vice recognition needs in terms of preprocessing?

slfink, 2018-10-09:
Browsing the µSpeech wiki, I stumbled across a walkthrough video for [calibrating the hardware.](https://www.youtube.com/watch?v=BctPULWywYY&list=PL3w3hv5y0WElFP5O4oShEj51Ur0D6h_D4)

He used a condenser microphone from an old toy (per the video comments) and a pre-amplifier. I'm not sure how well the microphones we'll be using will compare with what he has, but if they don't pick up anything we can build an amp and filter it if necessary.

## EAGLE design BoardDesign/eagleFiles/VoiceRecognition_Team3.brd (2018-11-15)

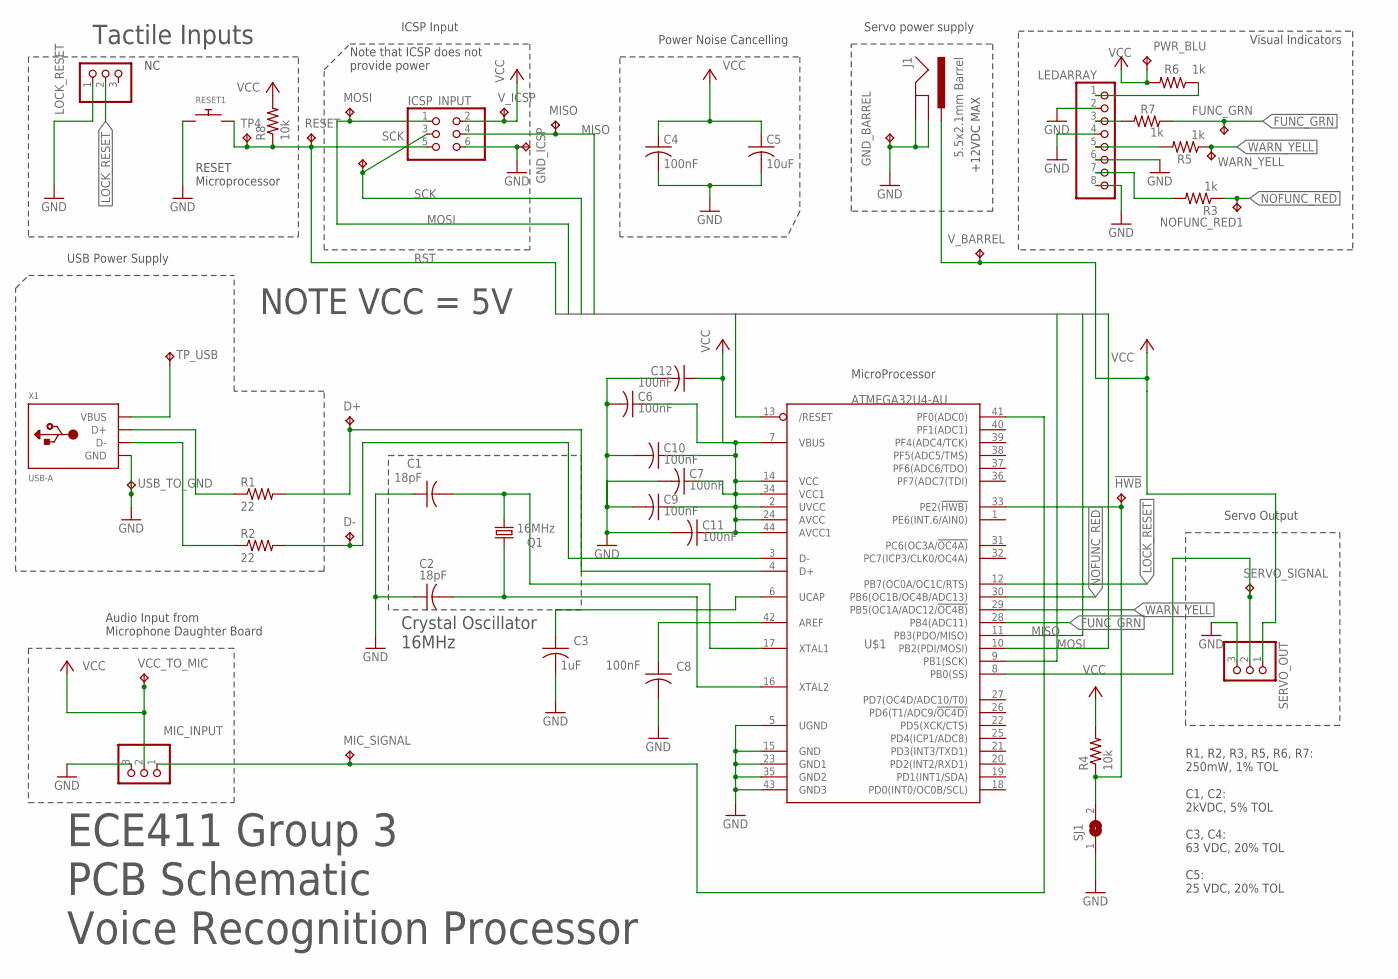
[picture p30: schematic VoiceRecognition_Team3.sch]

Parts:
!HWB: TPTP15SQ; TP15SQ
C1, C2: 18pF; C1206
C3: 1uF; C1206
C4, C6, C7, C8, C9, C10, C11, C12: 100nF; C1206
C5: 10uF; C1206
D+: TPTP15SQ; TP15SQ
D-: TPTP15SQ; TP15SQ
FUNC_GRN: TPTP15SQ; TP15SQ
GND_BARREL: TPTP15SQ; TP15SQ
GND_ICSP: TPTP15SQ; TP15SQ
ICSP_INPUT: PINHD-2X3; 2X03
J1: 5.5x2.1mm Barrel; POWER_JACK_SMD
LEDARRAY: PINHD-1X8BIG; 1X08-BIG
LOCK_RESET: PINHD-1X3; 1X03
MIC_INPUT: PINHD-1X3; 1X03
MIC_SIGNAL: TPTP15SQ; TP15SQ
MISO: TPTP15SQ; TP15SQ
MOSI: TPTP15SQ; TP15SQ
NOFUNC_RED1: TPTP15SQ; TP15SQ
PWR_BLU: TPTP15SQ; TP15SQ
Q1: 16MHz; CTS406
R1, R2: 22; M1206
R3, R5, R6, R7: 1k; M1206
R4, R8: 10k; M1206
RESET: TPTP15SQ; TP15SQ
RESET1: SWITCH_PUSHBUTTONC&K_KSS; BTN_CK_KSS
SCK: TPTP15SQ; TP15SQ
SERVO_OUT: PINHD-1X3; 1X03
SERVO_SIGNAL: TPTP15SQ; TP15SQ
SJ1: SJW
TP4: TPTP15SQ; TP15SQ
TP_USB: TPTP15SQ; TP15SQ
U$1: ATMEGA32U4-AU; TQFP44
USB_TO_GND: TPTP15SQ; TP15SQ
VCC_TO_MIC: TPTP15SQ; TP15SQ
V_BARREL: TPTP15SQ; TP15SQ
V_ICSP: TPTP15SQ; TP15SQ
WARN_YELL: TPTP15SQ; TP15SQ
X1: USB-A; MOLEX_480371000

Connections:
FUNC_GRN: FUNC_GRN.TP, R7.1, U$1.28 (PB4(ADC11))
GND: C1.1, C2.1, C3.2, C4.2, C5.2, C6.2, C7.2, C8.2, C9.2, C10.2, C11.2, C12.2, GND_BARREL.TP, GND_ICSP.TP, ICSP_INPUT.6, J1.GND (GNDBREAK), J1.P$4 (GND), LEDARRAY.2, LEDARRAY.4, LEDARRAY.6, LEDARRAY.8, LOCK_RESET.1, MIC_INPUT.3, RESET1.P$1, SERVO_OUT.3, SJ1.1, U$1.5 (UGND), U$1.15 (GND), U$1.23 (GND1), U$1.35 (GND2), U$1.43 (GND3), USB_TO_GND.TP, X1.4 (GND)
HWB: !HWB.TP, R4.1, SJ1.2, U$1.33 (PE2(!HWB))
LOCK_RESET: LOCK_RESET.2, U$1.12 (PB7(OC0A/OC1C/RTS))
MIC_SIGNAL: MIC_INPUT.1, MIC_SIGNAL.TP, U$1.41 (PF0(ADC0))
MISO: ICSP_INPUT.4, MISO.TP, U$1.11 (PB3(PDO/MISO))
MOSI: ICSP_INPUT.1, MOSI.TP, U$1.10 (PB2(PDI/MOSI))
unnamed: C3.1, U$1.6 (UCAP)
unnamed: C1.2, Q1.3 (2), U$1.17 (XTAL1)
unnamed: R1.1, X1.3 (D+)
unnamed: LEDARRAY.1, R6.1
unnamed: LEDARRAY.5, R5.2
unnamed: LEDARRAY.7, R3.2
unnamed: TP_USB.TP, X1.1 (VBUS)
unnamed: LEDARRAY.3, R7.2
unnamed: R2.1, X1.2 (D-)
unnamed: D+.TP, R1.2, U$1.4 (D+)
unnamed: C8.1, U$1.42 (AREF)
unnamed: D-.TP, R2.2, U$1.3 (D-)
unnamed: C2.2, Q1.1, U$1.16 (XTAL2)
NOFUNC_RED: NOFUNC_RED1.TP, R3.1, U$1.30 (PB6(OC1B/OC4B/ADC13))
RST: ICSP_INPUT.5, R8.1, RESET.TP, RESET1.P$2, TP4.TP, U$1.13 (/RESET)
SCK: ICSP_INPUT.3, SCK.TP, U$1.9 (PB1(SCK))
SIGNAL: SERVO_OUT.2, SERVO_SIGNAL.TP, U$1.8 (PB0(SS))
VCC: C4.1, C5.1, C6.1, C7.1, C9.1, C10.1, C11.1, C12.1, ICSP_INPUT.2, J1.VIN0 (PWR), MIC_INPUT.2, PWR_BLU.TP, R4.2, R6.2, R8.2, SERVO_OUT.1, U$1.2 (UVCC), U$1.7 (VBUS), U$1.14 (VCC), U$1.24 (AVCC), U$1.34 (VCC1), U$1.44 (AVCC1), VCC_TO_MIC.TP, V_BARREL.TP, V_ICSP.TP
WARN_YELL: R5.1, U$1.29 (PB5(OC1A/ADC12/!OC4B)), WARN_YELL.TP

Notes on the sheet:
MicroProcessor
Power Noise Cancelling
ICSP Input
Visual Indicators
Audio Input from Microphone Daughter Board
ECE411 Group 3 PCB Schematic Voice Recognition Processor
Servo Output
Note that ICSP does not provide power
Crystal Oscillator 16MHz
RESET Microprocessor
Tactile Inputs
Servo power supply
NOTE VCC = 5V
USB Power Supply
R1, R2, R3, R5, R6, R7: 250mW, 1% TOL C1, C2: 2kVDC, 5% TOL C3, C4: 63 VDC, 20% TOL C5: 25 VDC, 20% TOL
+12VDC MAX

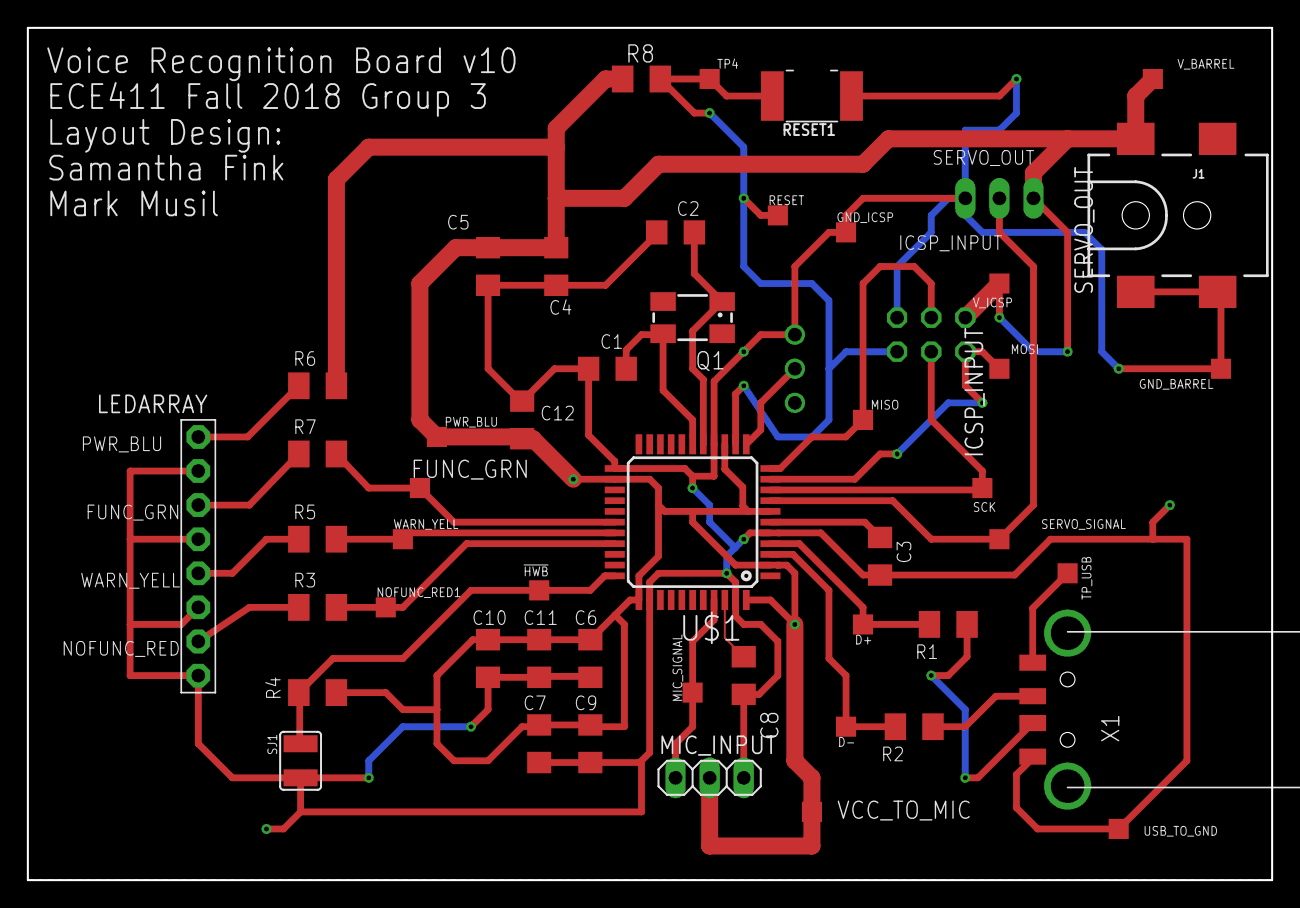
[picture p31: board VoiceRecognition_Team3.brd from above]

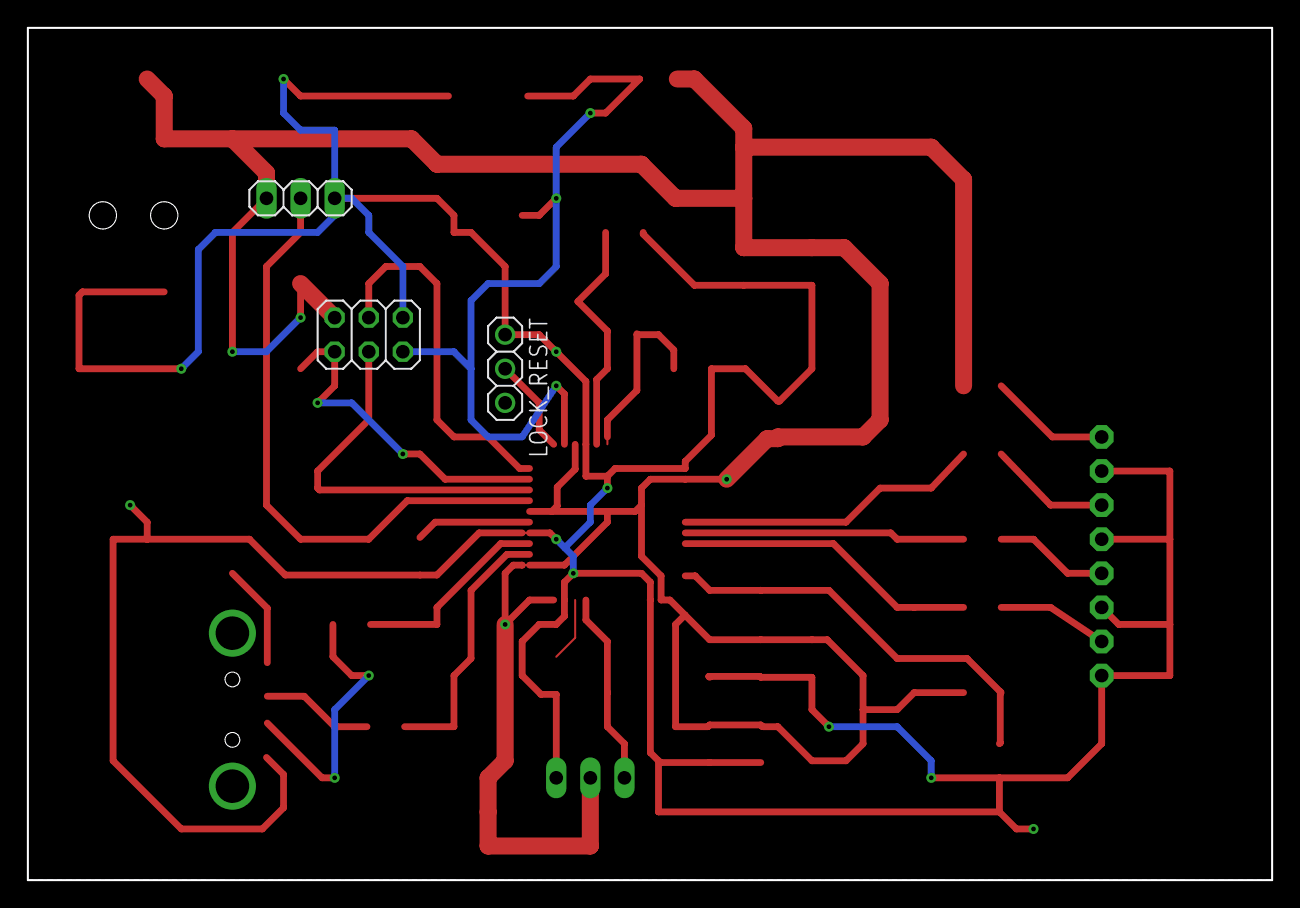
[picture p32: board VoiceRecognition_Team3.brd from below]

Board: 2 copper layers, 92.7 x 63.5 mm, 52 parts (3 on the bottom side), 26 nets.

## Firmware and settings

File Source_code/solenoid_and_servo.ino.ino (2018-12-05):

#include <Servo.h>
#include <uspeech.h>
//#define LED pins
  // #define yellow 9 yellow is power; do not need
  #define red 10
  #define green 8
  #define yellow 9
  #define button 11
signal voice(A5);
int time; // this calibrates our time for library use
bool first = true, word_waiting = false;
syllable syll; // name of our accumulator class
Servo lock_mechanism; // this is the name of our servo object 
int sum = 0;
int i = 0;

void setup(){ // This runs once on startup
  //########################################
  //#DEBUG STUFF, delete for final delivery#
  //#These were values we tried along the way. They didn't work at that time.
  //#voice.minVolume = 50; // was 600
  //#voice.econstant = 2; // this value never exceeds 1 good
  //#voice.aconstant = 4; // this value never exceeds 3, thinks it's o
  //#voice.fconstant = 300; // THIS VALUE BREAKS OUR STUFF
  //#voice.vconstant = 5; // doesn't exceed 4
  //#voice.shconstant = 8; // doesn't go under 8, goes 8-12
  //#voice.f_enabled = true; // THIS VALUE MAKES /f/ WORK AND EVERYTHING ELSE BREAKS
  //#voice.amplificationFactor = 2; // let's try to boost our signal
  //#######################################
  voice.minVolume = 200; // was 600
  voice.econstant = 2; // this value never exceeds 1 good
  voice.aconstant = 4; // this value never exceeds 3, thinks it's o
  voice.vconstant = 6; // doesn't exceed 4
  voice.shconstant = 8; // doesn't go under 8, goes 8-12
  voice.fconstant = 400;
  Serial.begin(9600);
  //time = millis(); // DEBUG THIS, it was placed in a different place in example
  voice.calibrate(); // call to calibrate function
  lock_mechanism.attach(17);
  pinMode(red, INPUT); 
  pinMode(yellow, OUTPUT); 
  pinMode(yellow, OUTPUT); 
  pinMode(green, OUTPUT);
  //digitalWrite(green, LOW);
  pinMode(button, OUTPUT);  
 }
 //This is the unlock function; it just writes to the servo.
void unlock(){
  digitalWrite(green, HIGH);
  lock_mechanism.write(0); //make sure this works, it should go 90 degrees to the right 
  Serial.println("This is a debug statement to prove that unlock worked.");
}
 //This is the lock function, to be triggered when the user pushes a button on the lid
void lock(){
  lock_mechanism.write(90); // returns to the center
  digitalWrite(green, LOW);
  Serial.println("This is a debug statement to prove that lock worked.");
}
 void loop(){
 // while(true){
  // ###############################################################
  // # This loop tests for silence. If it's silent it checks the last thing it heard when
  // # it wasn't silent. If it isn't silent it starts accumulating phonemes for testing.
  // # After testing a word, it should clear the accumulators and set word_waiting to false.
  // # This keeps it from holding on to garbage phonemes.
  // # This also means that the word is only tested after you stop talking.
  // # Test for the presence of the password ("sesame" or "seesaw")
  // ################################################################
    //int i = 0;
   // digitalWrite(red, HIGH);
   //   delay(200);
    //  digitalWrite(red, LOW);
     
    //  Test for the presence of the button
    if(digitalRead(red)){
      lock();
      
      //delay(200);
      //digitalWrite(red, LOW);
      //delay(200);
    }
    
    char a_phoneme = voice.getPhoneme(); //listen for and collect a word
    //syll.debugPrint();
  // Serial.println(voice.getPhoneme()); // print the phoneme you got for debugging
    if(a_phoneme == ' ') {
      //digitalWrite(green, HIGH);
      //delay(200);
      //digitalWrite(green, LOW);
      //delay(200);
      if (word_waiting){
         sum = syll.f+syll.o+syll.v+syll.s+syll.h+syll.e;
        //digitalWrite(yellow, HIGH);
      //delay(200);
       // digitalWrite(yellow, LOW);
     // delay(200);
        if (sum > 90){
          syll.debugPrint();
          Serial.println(voice.getPhoneme()); // print the phoneme you got for debugging
          if (syll.s > 4){
                    if(syll.e > 30){
                                  i = 0;
                                  unlock(); 
                    }
                    else{
                      if(syll.v > 3)
                            unlock();
                    }
          }else{
                          i = 0;

                          if(syll.h < 4)
                          unlock();
                          while( i <= 3){
                         // digitalWrite(red, HIGH);
                         // delay(200);
                         // digitalWrite(green, HIGH);
                         // delay(200);
                         // digitalWrite(green, LOW);
                          //digitalWrite(red, LOW);
                          i++;
                          }
                        }
       }

      syll.f = 0;
      syll.e = 0;
      syll.o = 0;
      syll.v = 0;
      syll.s = 0;
      syll.h = 0;     
      word_waiting = false;      
    }
 }
  else{
          if(first){
             time = millis();
          }
          syll.classify(a_phoneme);
            word_waiting = true;
 
    }    
  //}
}

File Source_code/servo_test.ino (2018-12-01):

/* Sweep
 by BARRAGAN <http://barraganstudio.com>
 This example code is in the public domain.

 modified 8 Nov 2013
 by Scott Fitzgerald
 http://www.arduino.cc/en/Tutorial/Sweep
*/

#include <Servo.h>

Servo myservo;  // create servo object to control a servo
// twelve servo objects can be created on most boards

int pos = 0;    // variable to store the servo position

void setup() {
  myservo.attach(10);  // attaches the servo on pin 9 to the servo object
  //myservo.write(0);
  delay(2000);
}

void loop() {
  for (pos = 0; pos <= 180; pos += 1) { // goes from 0 degrees to 180 degrees
    // in steps of 1 degree
    myservo.write(pos);              // tell servo to go to position in variable 'pos'
    delay(10);                       // waits 15ms for the servo to reach the position
  }
  for (pos = 180; pos >= 0; pos -= 1) { // goes from 180 degrees to 0 degrees
    myservo.write(pos);              // tell servo to go to position in variable 'pos'
    delay(10);                       // waits 15ms for the servo to reach the position
  }
//    myservo.write(180);
//    delay(2000);
//    myservo.write(90);
//    delay(2000);
}

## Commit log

2018-10-05 The firs commit, it contains the bill of materials. Please leave commit notes, thank you
    [BillOFMaterials.ods]
2018-10-05 Added about 9 components to the BOM
    [BillOFMaterials.ods]
2018-10-10 Update BillOFMaterials.ods
    Added op-amp information. Also changed formatting so all monetary values had dollar signs because I'm a stickler.
    [BillOFMaterials.ods]
2018-10-10 Update BillOFMaterials.ods
    Corrected price for LM386; numbers are difficult late at night.
    [BillOFMaterials.ods]
2018-10-11 New BOM
    [BillOFMaterials.ods]
2018-10-12 Update BillOFMaterials.ods
    * Changed "Prototype" tab to "Final Product" tab.
    * Added Prototype materials, including purchase date.
    * Updated "Admin" tab to include more purchase information, and to allow the spreadsheet to keep a running tally of individual purchase values.
    [BillOFMaterials.ods]
2018-10-13 New bill of materials is up
    [BillOFMaterials.ods]
2018-11-01 Brought sanity back to our git
    [BackUp.brd, BackUp.sch, BillOFMaterials.ods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]
2018-11-02 Add files via upload
    Arjo Chakavarty's phoneme table for calibration and debugging using the Debug sketch in USpeech 4.0
2018-11-02 Add files via upload
    Phoneme reference output table for debugging and calibrating uSpeech on a given Arduino Uno.
2018-11-03 PCB Schematic completed
    [BillOFMaterials.ods, VoiceRecognition.brd, VoiceRecognition.sch]
2018-11-03 Organized the file structure of this repository
    [BackUp.brd, BackUp.sch, BillOFMaterials.ods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]
2018-11-03 Performed the schematic ERC
    [VoiceRecognition.sch]
2018-11-04 Completed the version 1 BOM
    [BillOFMaterials.ods, BillOFMaterials_old.ods, VoiceRecognitionGroup3.brd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]
2018-11-04 Some organization and file management
    [VoiceRecognitionGroup3_BOM_V1.ods, VoiceRecognitionGroup3_BOM_V1.xlsx]
2018-11-07 Board Update and Misc
    * Uploaded PCB board layout for review.
    * Updated names of some components to make them easier to identify on the schematic (LEDs, test points, etc.).
    [VoiceRecognition_Team3.brd, VoiceRecognition_Team3.sch]
2018-11-08 Added Updated Board and BOM, note this will not be the final revision
    [VoiceRecognitionGroup3_BOM_V1.ods, VoiceRecognitionGroup3_BOM_V1.xlsx, VoiceRecognition_Team3.brd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]
2018-11-08 Added a few changes to the board per andrew's suggestion
    [VoiceRecognitionGroup3_BOM_V1.ods, VoiceRecognitionGroup3_BOM_V1.xlsx, VoiceRecognition_Team3.brd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]
2018-11-08 Added a connection to ground in the USB jack
    [VoiceRecognition_Team3.brd, VoiceRecognition_Team3.sch]
2018-11-09 yeah
    * rearranged bypass caps to VCC
    * Added tolerances to bottom right of schem
    [VoiceRecognition_Team3.brd, VoiceRecognition_Team3.sch]
2018-11-09 VCC caps + cosmetics
    * Moved vcc bias caps onto board.
    * Moved component names/values around for legibility.
    * Rerouted some wires for cosmetic purposes.
    [VoiceRecognition_Team3.brd, VoiceRecognition_Team3.sch]
2018-11-09 Add files via upload
    Algorithm for final uspeech servo control code
2018-11-10 Vias & Ground Plane
    *Verified that all vias tied to GND were stiched. Wondering if we need additional ground stitching vias around the board?
    [VoiceRecognition_Team3.brd, VoiceRecognition_Team3.sch]
2018-11-10 Purchased the completed BOM and thus updated the transaction history on the BOM to reflect the dollars amounts contributed by each member
    [BillOFMaterials.ods, BillOFMaterials_old.ods, VoiceRecognitionGroup3_BOM_V1.ods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]
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2018-11-13 Update servocontrol_rawan.ino
    fixed errors made button work
    [servocontrol_rawan.ino]
2018-11-13 Rearranges
    * Moved some components around per Tom's suggestons. Edits from 11/12; forgot to push to git.,
    [VoiceRecognition_Team3.brd, VoiceRecognition_Team3.sch]
2018-11-14 Additional Board Updates
    *Moved C1 so signals N$2 and N$22 (from crystal oscillator) would connect directly to processor instead of through a via. Signal wire is now wider than previous versions of the layout.
    * Moved a few GND wires around.
    * Added two additional GND stitching vias.
    [VoiceRecognition_Team3.brd]
2018-11-15 Rearranged a few silkscreen labels on the layout
    [VoiceRecognition_Team3.brd]
2018-11-15 Moved items away from edge of board.
    Moved the following items:
    * SERVO_OUT, RESET button
    * TP GND
    * VCC at bottom of board between TP VCC and MIC_INPUT
    [VoiceRecognition_Team3.brd]
2018-11-15 Version number on board
    Put version number on board per oshpark instructions. Was not sure exactly what version it was; per Github, the file has been changed 10 times, so went with that.
    [VoiceRecognition_Team3.brd]
2018-11-15 I wanna die.
    Files with names designated for Oshpark upload.
    [ece411-t03-voice-recognizer.brd, ece411-t03-voice-recognizer.sch]
2018-11-15 asdf
    asdasfsadfsfd
    [ece411-t03-voice-recognizer.brd]
2018-11-15 Final final finalize finale of the final board layout
    [ece411-t03-voice-recognizer.brd]
2018-11-15 ERC/DRC Checks Complete on new board
    [ece411-t03-voice-recognizer.brd]
2018-11-15 Create finalcodePrototype
    This lets the servo open when you say shoar
2018-11-26 Added DXF files for cutting stencils
    tcream will be a stencil for the top of the board, while bcream should be for the back of the board (I don't think we need it).
    [ece411-t03-voice-recognizer-bcream.dxf, ece411-t03-voice-recognizer-tcream.dxf]
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2018-12-02 Add files via upload
    Where to ground ~HWB so that Arduino can upload to it via USB.
2018-12-02 Add files via upload
    Where to place rocker switch to conditionally switch off ~HWB
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2018-12-06 Organization and uploaded the presentation
    [BackUp.brd, BackUp.sch, BillOFMaterials.ods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]

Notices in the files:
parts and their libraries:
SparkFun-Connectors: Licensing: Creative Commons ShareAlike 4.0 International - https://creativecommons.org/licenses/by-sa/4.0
